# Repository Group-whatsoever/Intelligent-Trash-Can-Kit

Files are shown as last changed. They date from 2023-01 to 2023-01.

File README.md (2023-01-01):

# Intelligent Trash Can Kit

## Introduction

**Core Functions**:

 - Capacity detection
 - Automatic notification
 - Automatic lid opening
 - Automatic bag sealing

**Goal**:

 - Bring intelligence to outdoor trash cans at a low cost.

**Problems Solved**:

 - Cleaning staff must regularly check to make sure that the trash cans are not full.
   - Solved by **Capacity detection** and **Automatic notification**.
 - People have a habit of continuing to throw trash into trash cans that are already nearly full and left open, causing them to overflow.
   - Solved by **Automatic lid opening** and **Automatic bag sealing**

## Poster



## Authors

This project is brought to you by Group 4 in the SDM 242 course during the Fall 2022 semester.

**Group 4 Members**:
 - [DreamWalkerXZ](https://github.com/DreamWalkerXZ)
 - [drinktoomuchsax](https://github.com/drinktoomuchsax)
 - [Doveqise](https://github.com/Doveqise)
 - [David-s2029](https://github.com/David-s2029)

## Credits

- [Using a Raspberry Pi distance sensor (ultrasonic sensor HC-SR04)](https://tutorials-raspberrypi.com/raspberry-pi-ultrasonic-sensor-hc-sr04/)
- [Control a Stepper Motor using Python and a Raspberry PI](https://danielwilczak101.medium.com/control-a-stepper-motor-using-python-and-a-raspberry-pi-11f67d5a8d6d)
- [Ultrasonic Sensor HC-SR04](https://grabcad.com/library/ultrasonic-sensor-hc-sr04-3)
- [IR Sensor](https://grabcad.com/library/ir-sensor-7)
- [IR Sensor Module Circuit](https://circuitdigest.com/electronic-circuits/ir-sensor-circuit-diagram)
- [IR333 PT333 Module](https://oshwhub.com/jixin/project-43d72fd6c5764f3abb0b2004313ffb05)

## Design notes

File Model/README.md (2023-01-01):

# Model

| File | Description |
| :--- | :--- |
| Assembly.STEP | AP214 STEP file |
| Assembly.SLDASM | SolidWorks Assembly File |
| Assembly_* | Parts in SolidWorks Assembly File |

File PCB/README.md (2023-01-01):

# PCB

We used the module ["InfraredElude PT333"](https://oshwhub.com/jixin/project-43d72fd6c5764f3abb0b2004313ffb05) from OSHWHub, whose schematic and PCB fabrication files are included in this repository, because the course requires the use of operational amplifiers.

| File | Description |
| :--- | :--- |
| Schematic_InfraredElude_PT333.pdf | Schematic |
| Gerber_InfraredElude_PT333.zip | PCB fabrication files in Gerber format |
| BOM_InfraredElude_PT333.xlsx | Bill of materials |



截屏2023-01-01 16.14.48.png

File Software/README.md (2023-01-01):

# Software

## Connect wires

| Raspberry Pi 4 Model B (Board Numbering) | External Devices' Pins |
| --- | --- |
| 12 | Ultrasonic Sensor's Trigger Pin |
| 18 | Ultrasonic Sensor's Echo Pin |
| 11 | LED Pin |
| 33 | Stepper Motor Driver's Enable Pin |
| 31 | Stepper Motor Driver's Direction Pin |
| 29 | Stepper Motor Driver's Pulse Pin |
| 16 | Infrared Sensor's Output Pin |

## Install dependencies

> The following commands were only tested on Raspberry Pi OS (Release date: September 22nd 2022, System: 64-bit, Kernel version: 5.15, Debian version: 11)

```shell
sudo apt update
sudo apt upgrade
sudo apt install python3-pip
sudo pip3 install RPi.GPIO
```

## Adjust `config.ini`

```shell
cd THIS_SOFTWARE_DIRECTORY
# Tune stepper motor's parameters (OpenDirection, Steps, Delay)
python3 utils/stepper_motor.py
# Tune ultrasonic sensor's parameters (CriticalDistance)
python3 utils/ultrasonic_sensor.py
# Use your favorite tool to adjust those parameters in config.ini
vim config.ini
```

## Run the software

```shell
cd THIS_SOFTWARE_DIRECTORY
python3 start.py
```

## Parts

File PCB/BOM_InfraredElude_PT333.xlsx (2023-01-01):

ID | Name | Designator | Footprint | Quantity | BOM_Supplier
1 | 100nF/50V | C1,C2 | 0603_C_JX | 2 | LCSC
2 | Red/LED | LED1 | 0603_D_JX | 1 | LCSC
3 | Green/LED | LED2 | 0603_D_JX | 1 | LCSC
4 | M_2.54_1*3P_Angled_JX | P1 | M_2.54_1*3P_JX | 1 | LCSC
5 | 10K/1% | R1,R4,R5,R6 | 0603_R_JX | 4 | LCSC
6 | 3362P_10K | R2 | RES-ADJ_3362P_JX | 1 | LCSC
7 | 100R/1% | R3 | 0603_R_JX | 1 | LCSC
8 | IR333_JX | U2 | LED_5_H_JX | 1 | LCSC
9 | PT333_JX | U3 | BJT_5_H_JX | 1 | LCSC
10 | LM393DT_JX | U1 | SOP8_150MIL_JX | 1 | LCSC

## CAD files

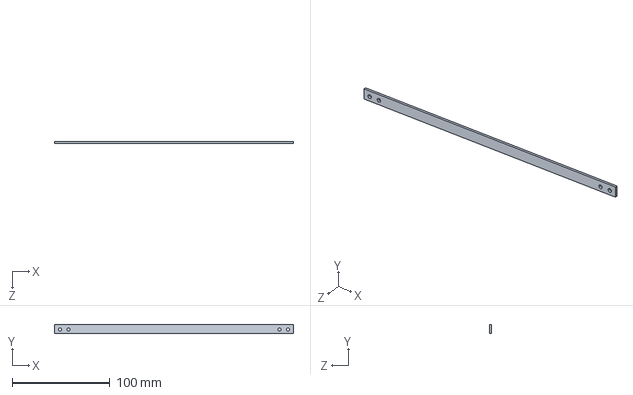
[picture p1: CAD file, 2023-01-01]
Model/Assembly_inner-plate-245.SLDPRT
245.0 x 9.00 x 2.00 mm

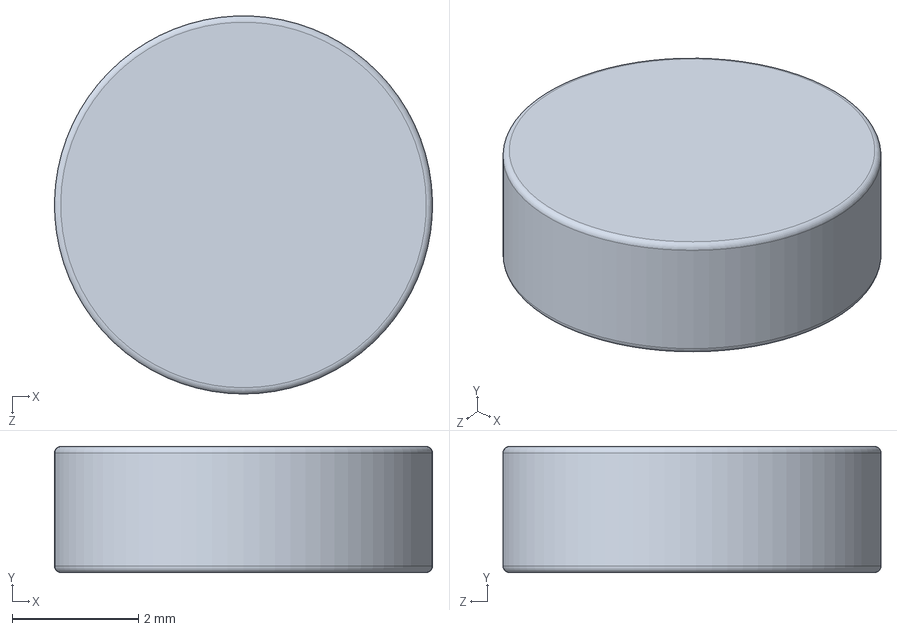
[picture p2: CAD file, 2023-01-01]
Model/Assembly_magnet.SLDPRT
6.00 x 2.00 x 6.00 mm

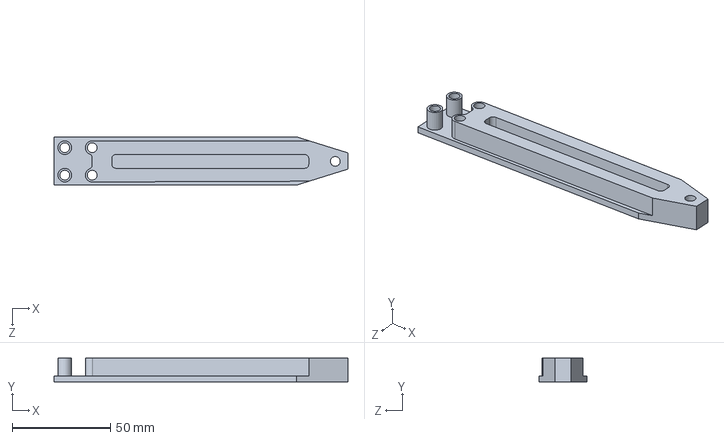
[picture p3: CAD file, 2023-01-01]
Model/Assembly_杠杆_再设计.SLDPRT
150.0 x 12.0 x 24.6 mm

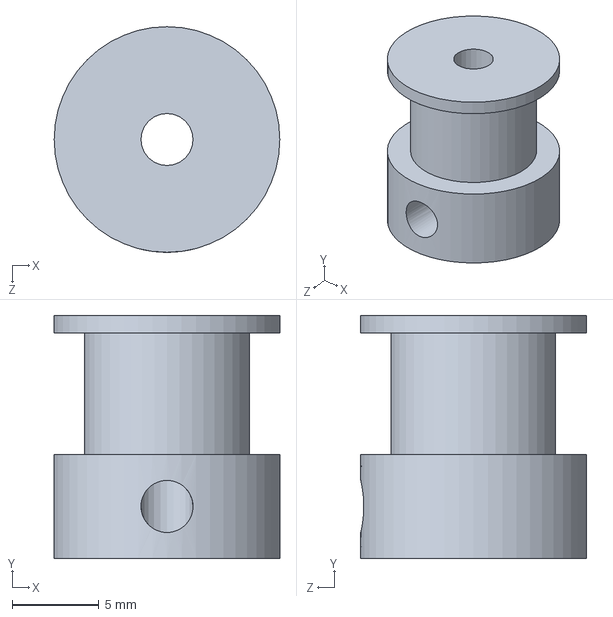
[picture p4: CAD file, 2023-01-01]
Model/Assembly_Synchronous-wheel.SLDPRT
13.0 x 14.0 x 13.0 mm

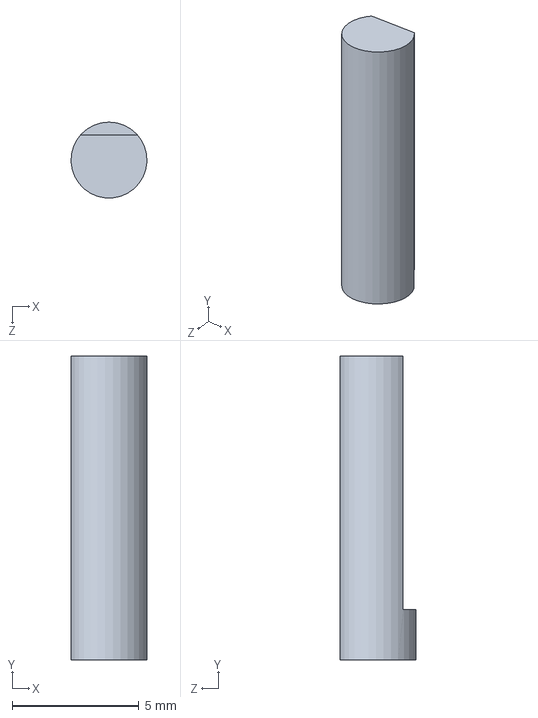
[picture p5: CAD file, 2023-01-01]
Model/Assembly_n20_shaft.SLDPRT
3.00 x 12.0 x 2.99 mm

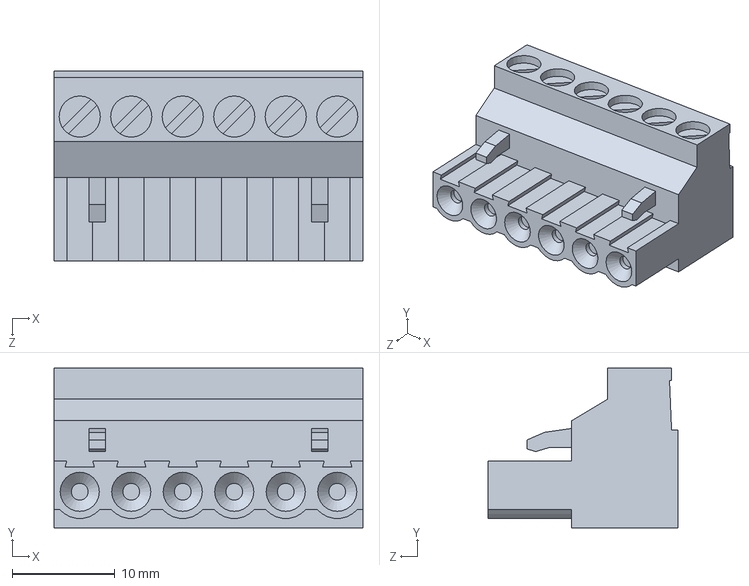
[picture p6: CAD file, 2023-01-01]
Model/Assembly_Eurostyle Terminal Block 6 Pos 5.0 mm RA Plug, SMAKN TB6600 Stepper Motor Driver.SLDPRT
30.0 x 15.5 x 18.4 mm

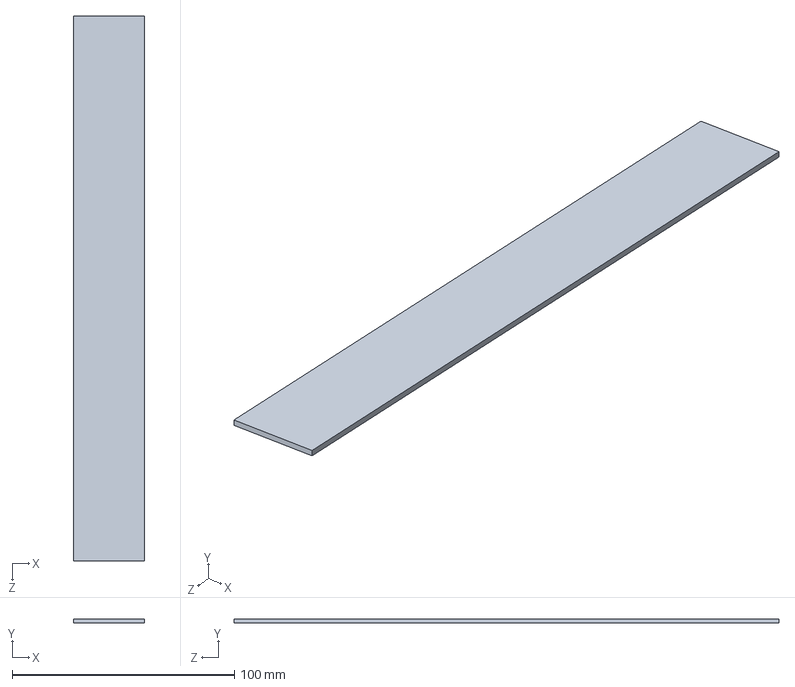
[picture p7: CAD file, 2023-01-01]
Model/Assembly_side-plate-forHS-v0.SLDPRT
32.0 x 2.00 x 245.0 mm

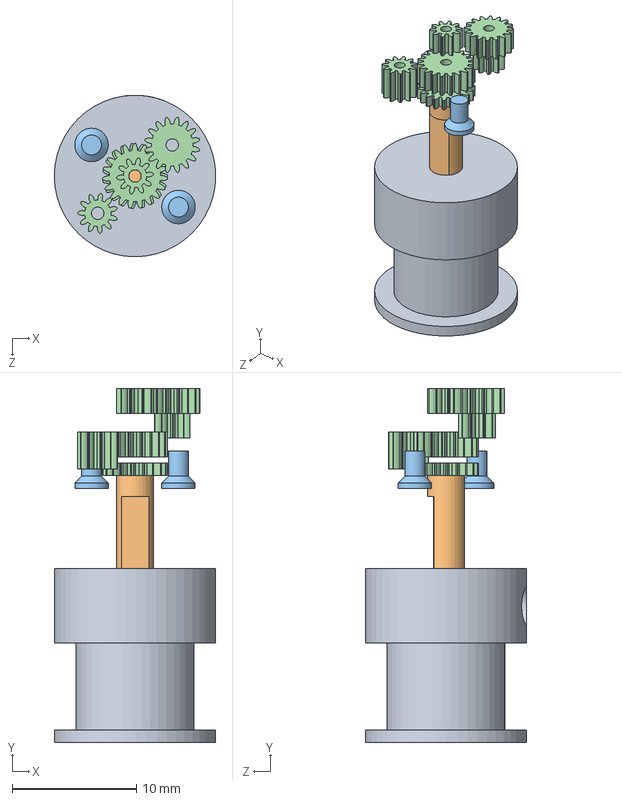
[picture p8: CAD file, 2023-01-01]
Model/Assembly_fixed-Motor.SLDASM
13.0 x 28.5 x 13.0 mm
Assembly_n20_shaft
cross recessed countersunk head screws gb1 x 2
spur gear_gb x 6
Assembly_Synchronous-wheel

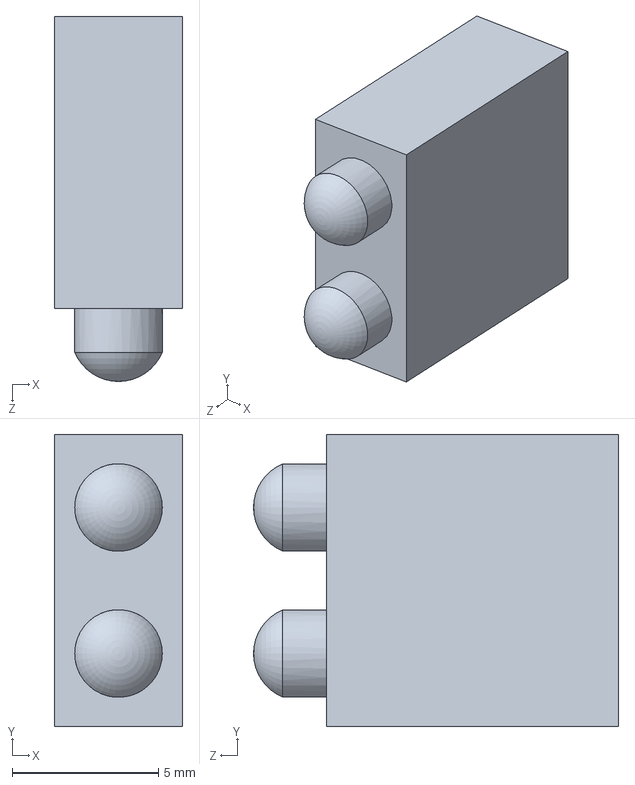
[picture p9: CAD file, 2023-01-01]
Model/Assembly_LED Body, SMAKN TB6600 Stepper Motor Driver.SLDPRT
4.40 x 10.0 x 12.5 mm

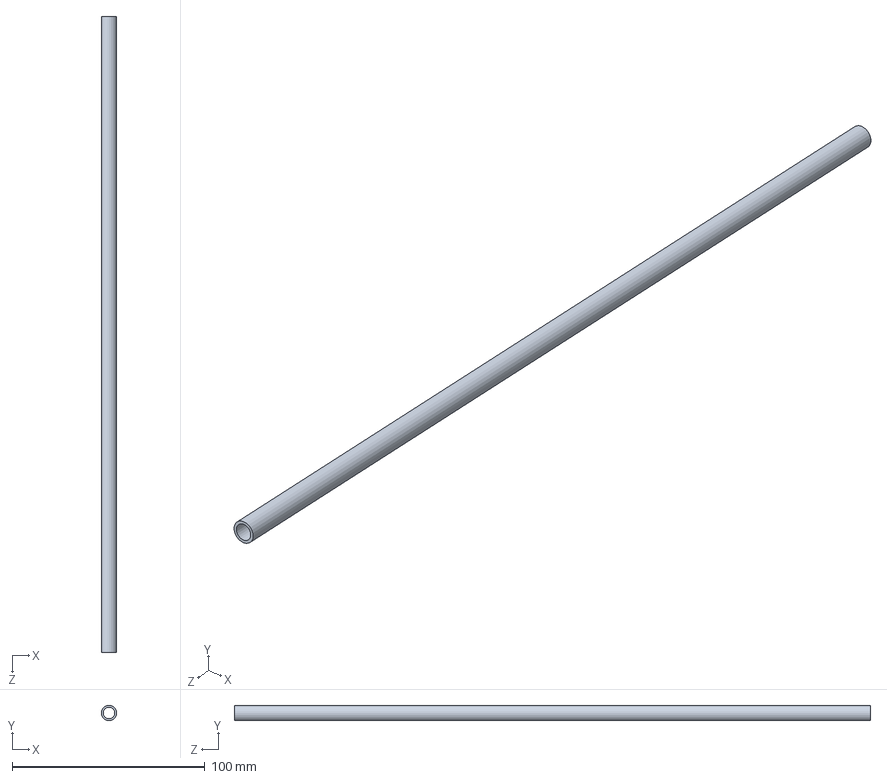
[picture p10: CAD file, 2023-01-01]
Model/Assembly_carbon-rob-long.SLDPRT
8.00 x 8.00 x 330.0 mm

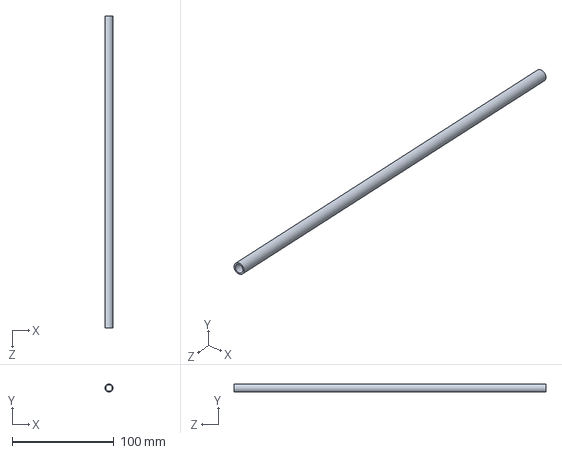
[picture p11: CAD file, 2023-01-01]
Model/Assembly_carbon-rob.SLDPRT
8.00 x 8.00 x 306.0 mm

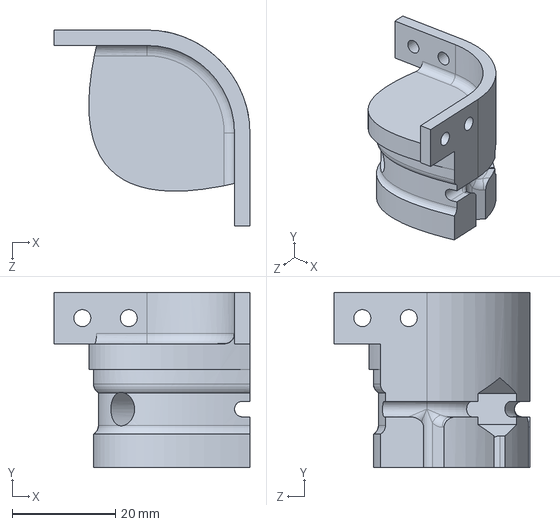
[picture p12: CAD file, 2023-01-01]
Model/Assembly_heat-cut-by-czy.SLDPRT
38.0 x 34.0 x 38.0 mm

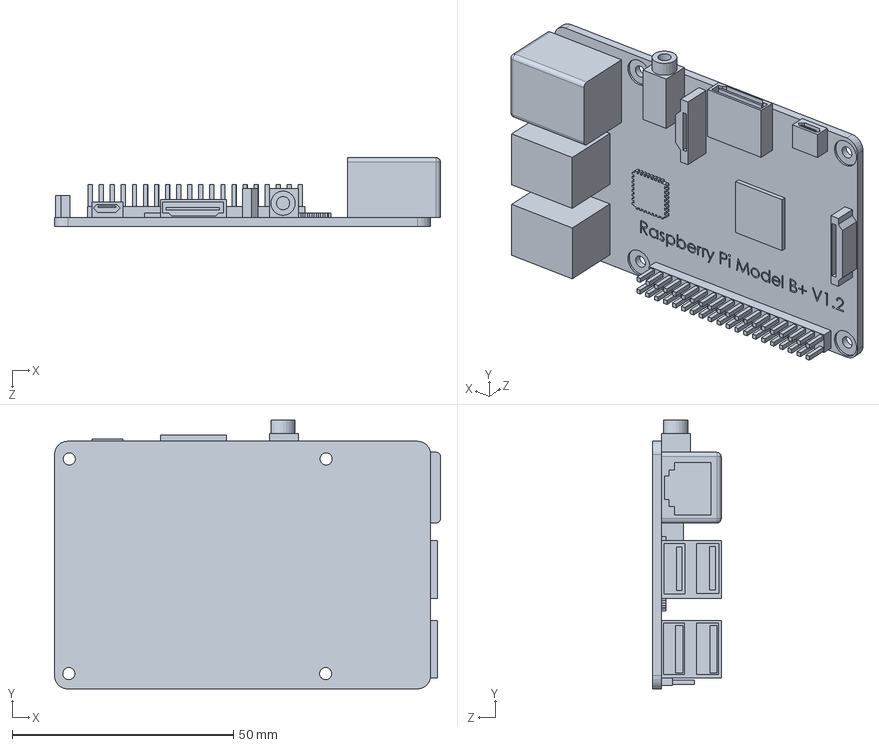
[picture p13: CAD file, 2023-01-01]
Model/Assembly_树莓派.SLDPRT
87.2 x 60.8 x 15.5 mm

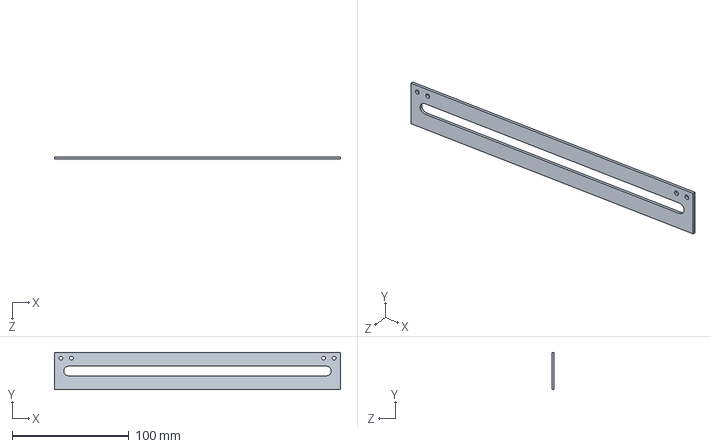
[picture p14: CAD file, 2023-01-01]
Model/Assembly_inner-plate-high.SLDPRT
245.0 x 32.0 x 2.00 mm

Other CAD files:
Model/Assembly_Eurostyle Terminal Block 4 Pos 5.0 mm RA Plug, SMAKN TB6600 Stepper Motor Driver.SLDPRT
Model/Assembly_moving-rob.SLDASM
Model/Assembly_moving-rob-connector.SLDPRT
Model/Assembly_bottum-corner-forHS-v0.SLDPRT
Model/Assembly_240L Wheelie Bin.SLDPRT
Model/Assembly_42电机.SLDPRT
Model/Assembly_DIP Switch, SMAKN TB6600 Stepper Motor Driver.SLDPRT
Model/Assembly_D形轴.SLDPRT
Model/Assembly_Eurostyle Terminal Block 2 Pos 5.0 mm RA Plug, SMAKN TB6600 Stepper Motor Driver.SLDPRT
Model/Assembly_Heatsink Style Mounting Plate, SMAKN TB6600 Stepper Motor Driver.SLDPRT
Model/Assembly_SMAKN TB6600 Stepper Motor Driver.SLDASM
Model/Assembly_Sheet Metal Enclosure, SMAKN TB6600 Stepper Motor Driver.SLDPRT
Model/Assembly_Sonar_Lid_2.SLDPRT
Model/Assembly_Synchronous-belt-fastener.SLDPRT
Model/Assembly_bottum-corner-v0.SLDPRT
Model/Assembly_bottum-plate-forHS-v0.SLDPRT
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

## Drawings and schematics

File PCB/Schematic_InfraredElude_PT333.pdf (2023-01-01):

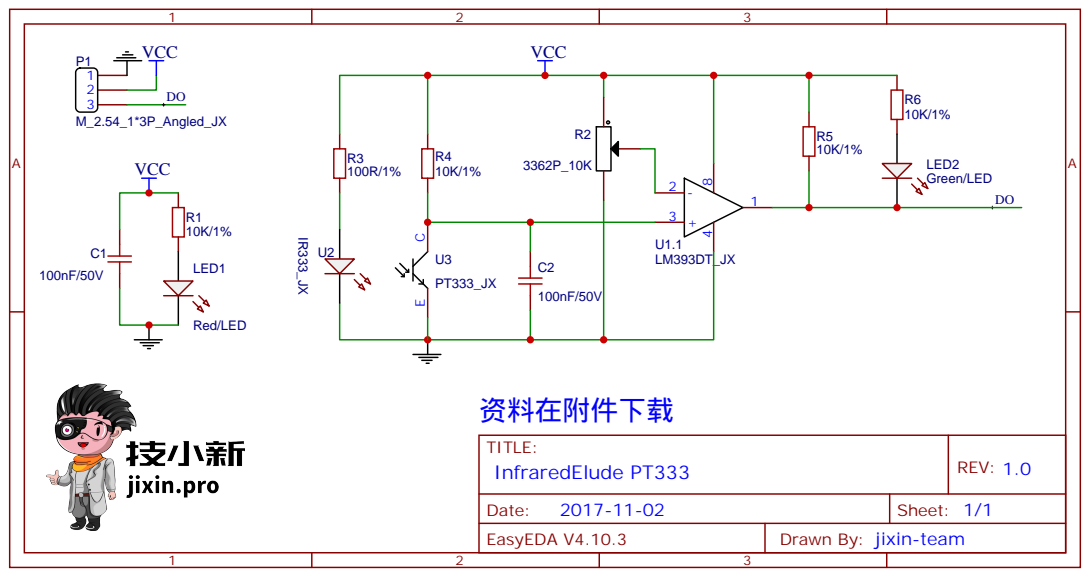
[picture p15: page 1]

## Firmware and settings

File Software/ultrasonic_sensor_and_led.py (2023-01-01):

import configparser
import RPi.GPIO as GPIO
import time

# GPIO Mode (BOARD / BCM)
GPIO.setmode(GPIO.BCM)

# set GPIO Pins
GPIO_TRIGGER = 18
GPIO_ECHO = 24

LED = 17

# set GPIO direction (IN / OUT)
GPIO.setup(GPIO_TRIGGER, GPIO.OUT)
GPIO.setup(GPIO_ECHO, GPIO.IN)

GPIO.setup(LED, GPIO.OUT)

config = configparser.ConfigParser()
config.read("config.ini")
critical_distance = int(config["UltrasonicSensor"]["CriticalDistance"])


def distance():
    # set Trigger to HIGH
    GPIO.output(GPIO_TRIGGER, True)

    # set Trigger after 0.01ms to LOW
    time.sleep(0.00001)
    GPIO.output(GPIO_TRIGGER, False)

    StartTime = time.time()
    StopTime = time.time()

    # save StartTime
    while GPIO.input(GPIO_ECHO) == 0:
        StartTime = time.time()

    # save time of arrival
    while GPIO.input(GPIO_ECHO) == 1:
        StopTime = time.time()

    # time difference between start and arrival
    TimeElapsed = StopTime - StartTime
    # multiply with the sonic speed (34300 cm/s)
    # and divide by 2, because there and back
    distance = (TimeElapsed * 34300) / 2

    return distance


if __name__ == "__main__":
    try:
        while True:
            dist = distance()
            print("Ultrasonic Sensor: Measured Distance = %.1f cm" % dist)
            if dist > critical_distance:
                # write status to status.txt
                with open("status.txt", "w") as f:
                    f.write("0")
                print('LED: ON')
                GPIO.output(LED, GPIO.HIGH)
            else:
                with open("status.txt", "w") as f:
                    f.write("1")
                print('LED: OFF')
                GPIO.output(LED, GPIO.LOW)
            with open("distance.txt", "w") as f:
                f.write(str(dist))
            time.sleep(1)

    # Reset by pressing CTRL + C
    except KeyboardInterrupt:
        GPIO.cleanup()
        print("Ultrasonic Sensor and LED: Cleaned Up")

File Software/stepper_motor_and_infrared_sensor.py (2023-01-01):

import configparser
import RPi.GPIO as GPIO
from time import sleep

# Enable pin from controller
EN = 33
# Direction pin from controller
DIR = 31
# Step pin from controller
STEP = 29
# 0/1 used to signify clockwise or counterclockwise.
CW = 1
CCW = 0

IR = 16

# Setup pin layout on PI
GPIO.setmode(GPIO.BOARD)

# Establish Pins in software
GPIO.setup(EN, GPIO.OUT)
GPIO.setup(DIR, GPIO.OUT)
GPIO.setup(STEP, GPIO.OUT)

# Set the enable pin to low to enable the stepper
GPIO.output(EN, 0)

# Set the first direction you want it to spin
GPIO.output(DIR, CW)

GPIO.setup(IR, GPIO.IN)

config = configparser.ConfigParser()
config.read("config.ini")
if config["StepperMotor"]["OpenDirection"] == "CW":
    open_direction = CW
    close_direction = CCW
else:
    open_direction = CCW
    close_direction = CW
steps = int(config["StepperMotor"]["Steps"])
delay = float(config["StepperMotor"]["Delay"])


def stepper(direction, steps, delay):
    # Set the direction you want it to spin
    GPIO.output(DIR, direction)
    # Run the stepper motor
    for x in range(steps):
        # Set one coil winding to high
        GPIO.output(STEP, GPIO.HIGH)
        # Allow it to get there.
        sleep(delay)  # Dictates how fast stepper motor will run
        # Set coil winding to low
        GPIO.output(STEP, GPIO.LOW)
        sleep(delay)  # Dictates how fast stepper motor will run


try:
    # Run forever.
    while True:
        status = 0
        with open("status.txt", "r") as f:
            status = f.read()
            print(status)
            if status == "":
                continue
            else:
                status = int(status)
        if GPIO.input(IR) == 0 and status == 0:
            print("Infrared Sensor: People Detected")
            print("Stepper Motor: Opening")
            stepper(open_direction, steps, delay)
            sleep(1)
            while GPIO.input(IR) == 0:
                sleep(1)
            print("Infrared Sensor: No People Detected")
            print("Stepper Motor: Closing")
            stepper(close_direction, steps, delay)

# Once finished clean everything up
except KeyboardInterrupt:
    GPIO.cleanup()
    print("Stepper Motor and Infrared Sensor: Cleaned Up")
